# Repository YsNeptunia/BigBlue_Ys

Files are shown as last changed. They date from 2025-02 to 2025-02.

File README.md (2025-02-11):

# BigBlue_Ys
自动捡乒乓球小车，我的电赛校赛选拔的题目。项目时间2024.6。
三人小队，我担任队长，负责方案整理、车体结构设计、32端下位机控制代码的编写、协调各成员分工等工作。

## 原题目
### 一、任务
设计并制作一个自动捡球小车，根据要求完成要求的任务。
### 二、要求
#### 1、基本要求
（1）小车从场地中央位置出发，能自主行驶。
（2）场地内随机放置10个乒乓球，小车能完成乒乓球的拾取，每拾取一个乒乓球发出声光指示信息。
（3）90秒内能完成10个乒乓球的拾取，并且全部存放在小车上。
（4）小车有相关信息的显示。
#### 2、发挥部分
 (1) 场地内随机放置10个乒乓球，5个白色5个橙色，小车从场地中央位置出发，拾取5个黄色乒乓球。
 (2) 拾取5个黄色乒乓球后，再完成5个白色乒乓球的拾取。
 (3) 以上过程不超过90秒，超时后所有动作不得分。
 (4) 场地内随机放置10个乒乓球，5个白色5个橙色，小车从场地中央位置出发，交替拾取不同颜色乒乓球，直到乒乓球全部拾取完，该过程不超过90秒，超时后所有动作不得分。
### 三、说明
#### 1、场地地面为1.5*1.5m的普通瓷砖地面，四周有高于2cm的围挡防止乒乓球出场地。
#### 2、小车允许用玩具车改装，但不能由人工遥控，和外接拉线供电和控制，其外围尺寸（含车体上附加装置）的限制为：长度≤20cm，宽度≤15cm。

## 实现过程
  首先，本题的最大难点不是控制，而是：如何在白色瓷砖地板上识别出白色的乒乓球。

  老师在题目讲解时认为我们用OpenMV调一下阈值就可以，可问题是，场地瓷砖是反光的，当灯光或者阳光照到地板上被反光时，OpenMV摄像头根本分辨不出乒乓球轮廓和地板（事实上，这也是很多其他人的难点，很多人也想当然在最后一个周用OpenMV识别结果失败）。用传统的图像处理思路是行不通了，在多次尝试后我们确定并验证了方案：
  **使用部署在嵌入式上位机中的神经网络视觉识别出白背景中的白球，上位机通过串口传回球中心在摄像头画面中的坐标，STM32下位机解算坐标，控制智能小车实现抓取乒乓球。**
  

  对于视觉部分，这部分的代码由有经验的队友1负责（队友2比较新手，我就让他负责上下位机通信协议部分了）。最初我们使用的嵌入式上位机是树莓派4b，但是其算力实在有限，精简后的YoloV5Lite算法只能跑到不到10帧，这对于有时间要求的题目而言显然是远远不足的。
  后来我们尝试了英伟达的JetsonNano开发板，由于可以调用GPU，同样的算法在这个平台上可以达到稳定30帧，最终决定了该方案。
  

  对于结构部分，我自行测绘建模，3D打印了车体的底盘和机械臂等结构。使用减速电机控制小车运动，连接上位机的摄像头对场地内的球进行寻找，当摄像头识别到球在指定位置后用舵机控制机械臂下压，用矿泉水瓶和橡皮筋制作类似网兜的结构将地上的球框柱，运送到高处使球自己滚落到车体上的收集框中。同时由于有球数量计数要求，我在机械臂上安装了一个光电门进行计数，相比只计数下压次数而言，这种方案显然更合理。（只计算下压次数有可能错漏导致无法拾起所有球）
  
  

  对于控制部分，依然使用了我较为熟悉的PID算法，在接收到上位机传来的xy坐标后32下位机控制两轮电机，到达位置后实行抓取操作。题目有三种抓球顺序所以我也设计了三种抓球模式。曾经担心卡轮子等潜在问题，在小车前安装了一个测距传感器，后来发现其实不需要。

https://github.com/user-attachments/assets/106b4148-775f-4484-b51f-987c8159d40d

  从立项到最终完成时间大约一个月。最终可以实现稳定在90秒内抓取所有球。

  ## 说明
  ### Car压缩包内为32下位机的代码工程文件，使用STM32CubeMX的HAL库开发，环境为Keil5和VS Code等。
  ### onnxruntime1压缩包内为上位机的yolov5代码和串口通信代码。环境为Jetson Nano中的Linux系统，安装Pytorch等。
  ### STL文件夹为小车的建模工程文件。

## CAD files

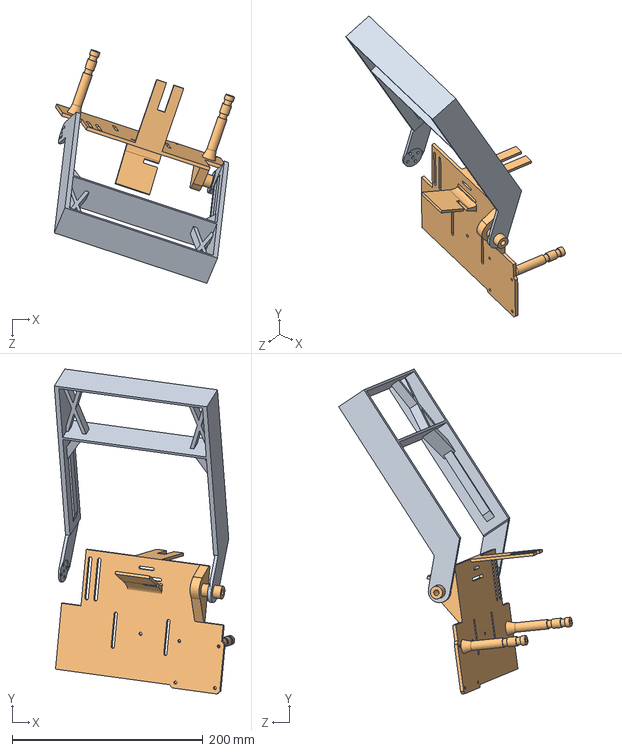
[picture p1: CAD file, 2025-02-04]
STL/装配体1.SLDASM
189.3 x 340.9 x 245.1 mm
BigBlue_V1.0(arm)
BigBlue_V1.0(deck)

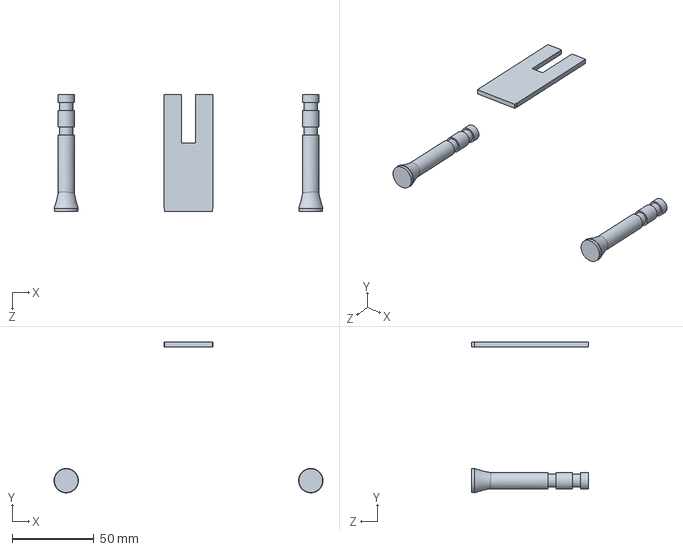
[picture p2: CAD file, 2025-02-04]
STL/BigBlue_V1.1(deck_2).SLDPRT
165.0 x 92.4 x 72.0 mm

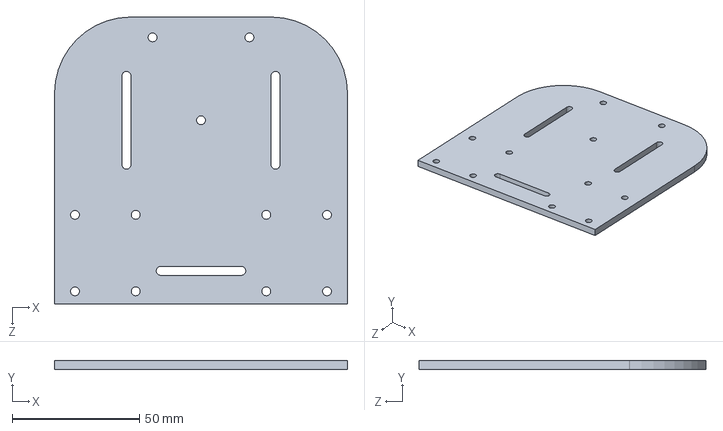
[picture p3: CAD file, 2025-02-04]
STL/BigBlue_V1.0(chassis).SLDPRT
115.3 x 3.60 x 112.9 mm

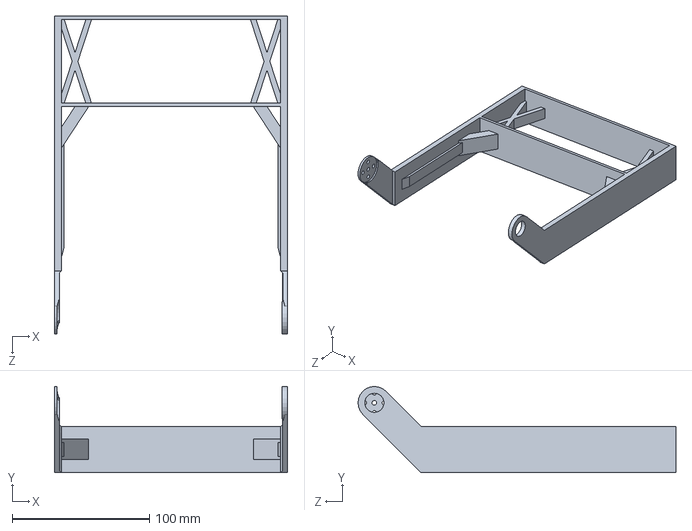
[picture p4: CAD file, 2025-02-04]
STL/BigBlue_V1.0(arm).SLDPRT
170.0 x 62.8 x 231.9 mm

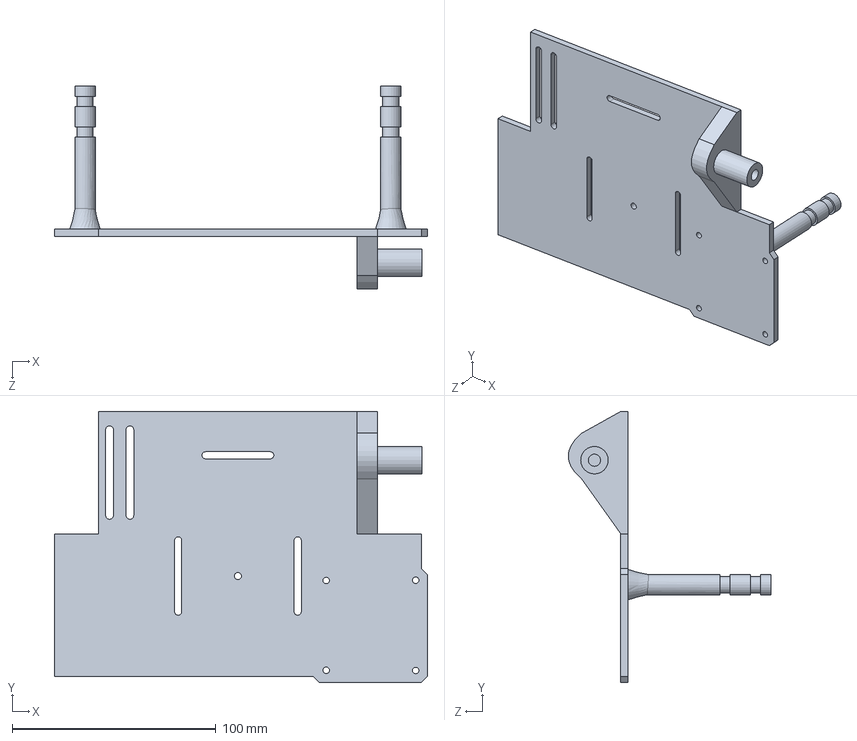
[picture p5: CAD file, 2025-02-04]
STL/BigBlue_V1.0.SLDPRT
183.0 x 133.0 x 99.4 mm

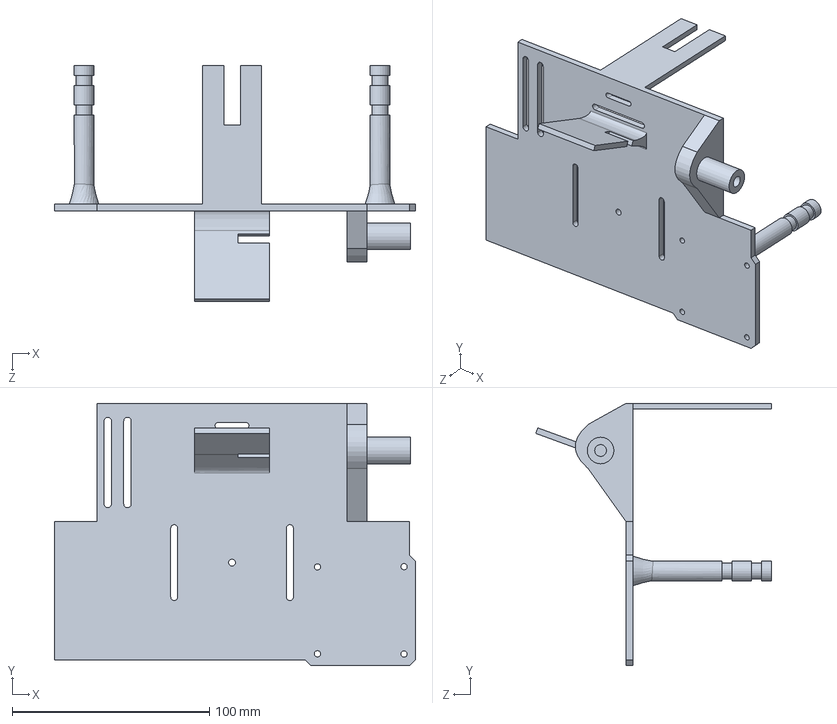
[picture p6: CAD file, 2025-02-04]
STL/BigBlue_V1.0(deck).SLDPRT
183.0 x 133.0 x 119.4 mm

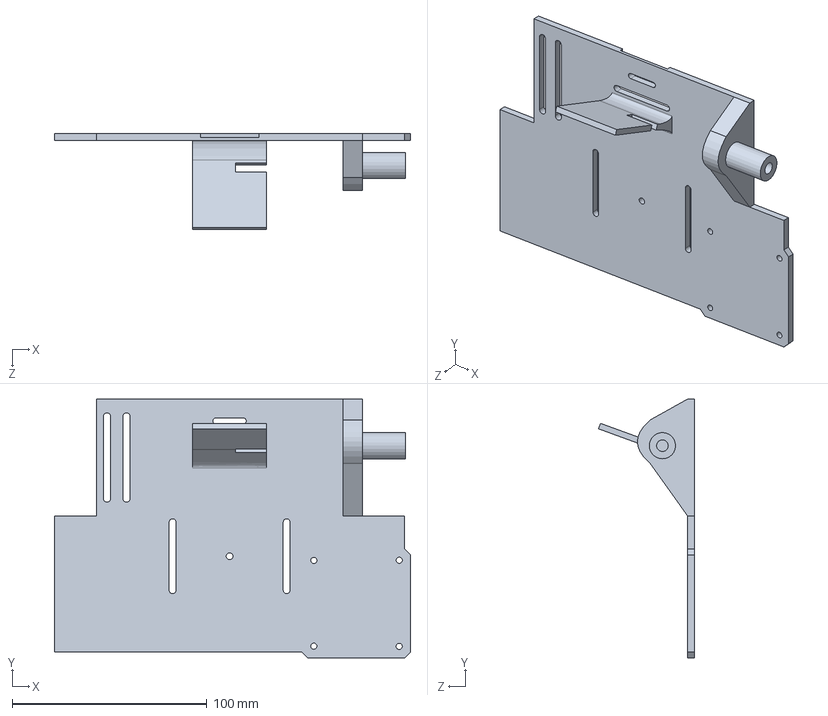
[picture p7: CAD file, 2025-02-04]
STL/BigBlue_V1.1(deck_1).SLDPRT
183.0 x 133.0 x 49.4 mm

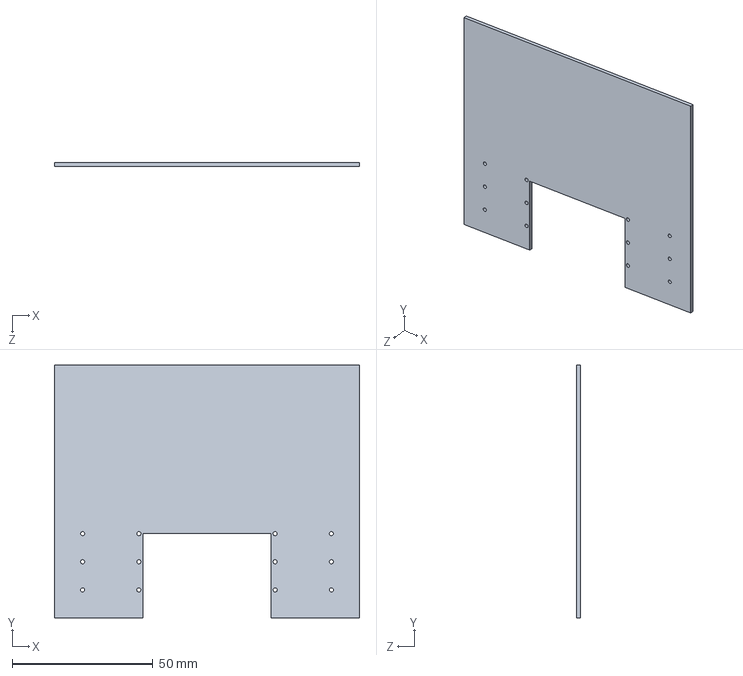
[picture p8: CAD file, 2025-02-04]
STL/零件2.SLDPRT
108.5 x 90.0 x 1.50 mm

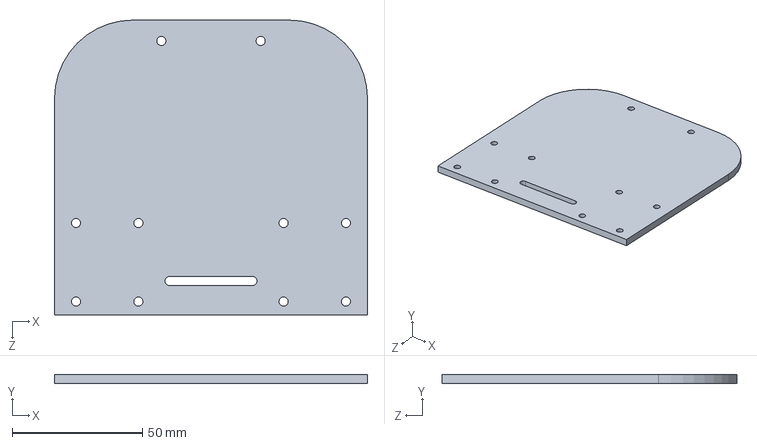
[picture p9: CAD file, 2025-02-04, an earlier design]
STL/BigBlue_V0.7.SLDPRT
120.0 x 3.60 x 113.0 mm

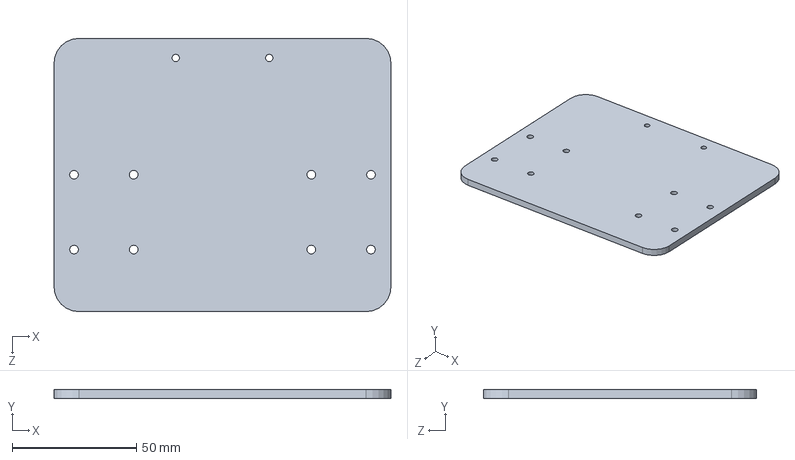
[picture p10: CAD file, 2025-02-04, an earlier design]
STL/BigBlue_V0.6.SLDPRT
135.5 x 3.60 x 109.9 mm

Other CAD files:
STL/BigBlue_V0.6.STL
STL/BigBlue_V0.7.STL
STL/BigBlue_V1.0(arm).STL
STL/BigBlue_V1.0(chassis).STL
STL/BigBlue_V1.0(deck).STL
STL/BigBlue_V1.1(deck_1).STL
STL/BigBlue_V1.1(deck_2).STL
